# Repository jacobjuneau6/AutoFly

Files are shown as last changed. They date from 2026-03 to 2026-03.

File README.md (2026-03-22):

# AutoFly
A cheap, light and, small autonomus drone with ~100g payload capacity and ardupilot
# Why
I made AutoFly as a successor to a pevious autonomus quadcopter that was not able to fly due to low power budgeting. With bigger motors and a 4X larger battery it should fly perfectly. I have always liked autonomus drones for the simple fact that it focuses entirely on design and tuning compared to FPV drones where the pilot plays a cirtical role.
# Assembly
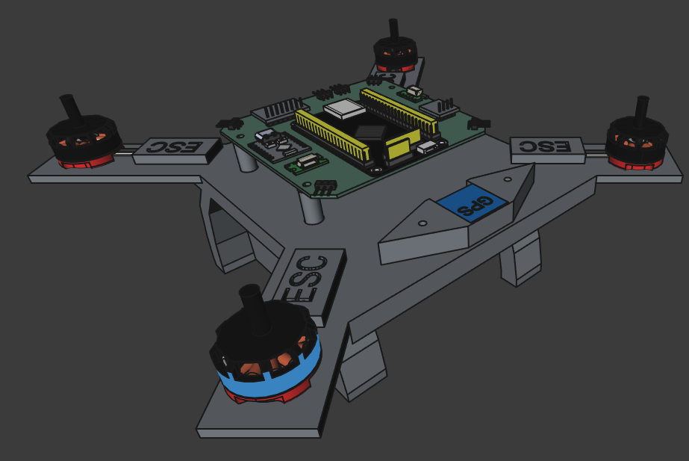
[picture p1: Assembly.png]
assembly photo

# PCB
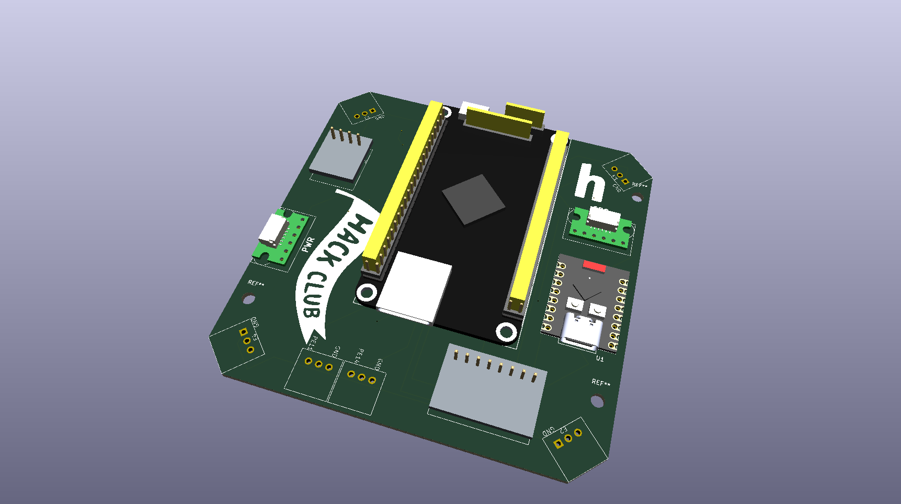
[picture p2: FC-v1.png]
pcb photo

# External Wiring
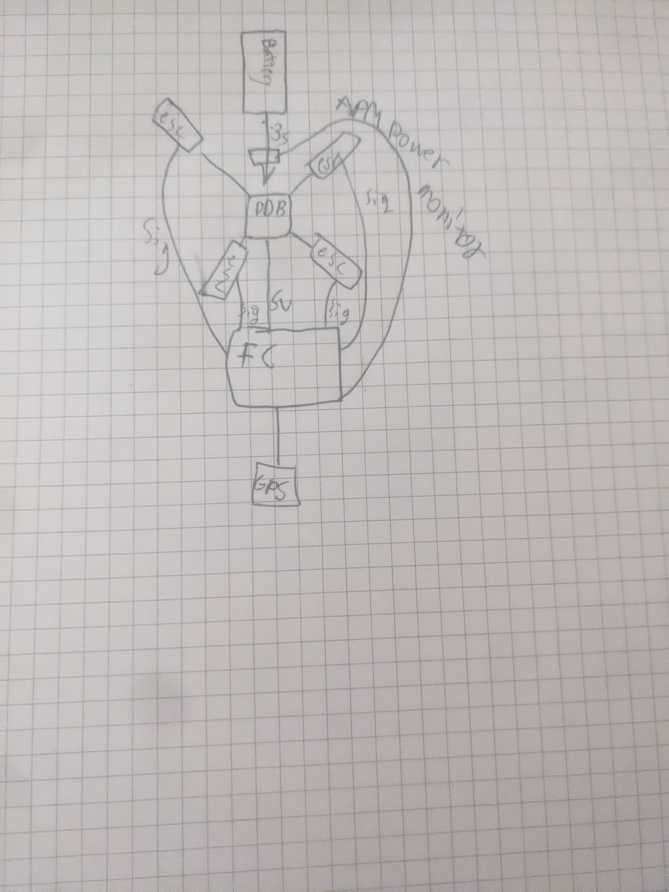
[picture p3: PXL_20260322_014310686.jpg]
hand drawn

# BOM
| Name | Purpose | Quantity | Total Cost (USD) | Link | Distributor |
| --- | --- | --- | --- | --- | --- |
| Custom PCB | hold all of the FC components | 1 | 12.50 |  | PCBWAY |
| Alibaba Shipping Customs and tax | Alibaba Shipping Customs and tax | 1 | 15.45 |  | Alibaba |
| Aliexpress shipping & tax | Aliexpress shipping & tax | 1 | 4.30 |  | Aliexpress |
| Amazon Shipping & TAX | Amazon Shipping & TAX | 1 | 7.67 |  | Amazon |
| M3 screws | hold down various components | 1 | 8.49 | https://www.amazon.com/Self-Tapping-Screws-Phillips-Carbon-Plastic/dp/B0BPM8J5F5 | Amazon |
| Deans T connectors | battery connector | 1 | 1.75 | https://www.aliexpress.us/item/3256806681263722.html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 | Aliexpress |
| 1mm pitch connectors | allows connecting standard drone peripherals to the FC | 1 | 13.22 | https://www.digikey.com/en/products/detail/pololu/4772/19529079 | Digikey |
| APM2.5 power monitor | measures the power and current off the battery to enter failsafe mode when battery about to die | 1 | 9.99 | https://www.amazon.com/Pixhawk-BEC-Helicopter-Quadcopters-Accessories/dp/B0BCJQR3YN?th=1 | Amazon |
| 3S lipo battery | powers the drone | 1 | 14.24 | https://www.amazon.com/OVONIC-Airplane-Quadcopter-Helicopter-Multi-Motor/dp/B077P73SDS?th=1 | Amazon |
| Propellers | provides the motors a way to generate lift | 1 | 16.99 | https://www.amazon.com/uxcell-Propellers-Quadcopter-Airplane-Adapter/dp/B07QK5CXK8 | Amazon |
| Power distribution board | sends power from the battery to all 4 escs | 1 | 4.51 | https://www.aliexpress.us/item/3256806649142265.html?mp=1 | Aliexpress |
| 2205 2300kv brushless motors | allows drone to fly  | 1 | 8.61 | https://www.aliexpress.us/item/3256808432301575.html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 | Aliexpress |
| BLHeli-s 20A ESCs | provides power and control to the motor | 1 | 29.61 | https://www.aliexpress.us/item/2255800001568515.html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 | Aliexpress |
| HGLRC M100-5883 GPS and Compass | Provides location and heading data to the FC | 1 | 18.99 | https://www.amazon.com/HGLRC-M100-5883-GPS-Generation-Compatible/dp/B0CB5N8RQ8 | Amazon |
| ESP32C3 super mini | Provides the transmitter and reciver | 1 | 9.99 | https://www.amazon.com/AITRIP-ESP32-C3-Development-Board-Bluetooth/dp/B0FBGDFPBQ?th=1 | Amazon |
| ICM-42688 IMU | Tells the drone its orientation and acceleration | 1 | 8.39 | https://www.alibaba.com/product-detail/AI-KSEN-Six-Axis-IMU-Module_1601663823996.html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 | Alibaba |
| GY-BMP280 | provides an altimeter | 1 | 0.43 | https://www.alibaba.com/product-detail/GY-BME280-5V-GY-BMP280-5V_1601291648398.html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 | Alibaba |
| STM32H743VIT6 | Will be the brains of the drone | 1 | 11.80 | https://www.alibaba.com/product-detail/STM32H743VIT6-STM32H750VBT6-STM32-STM32H-STM32H7-Core_1601368312109.html | Alibaba |

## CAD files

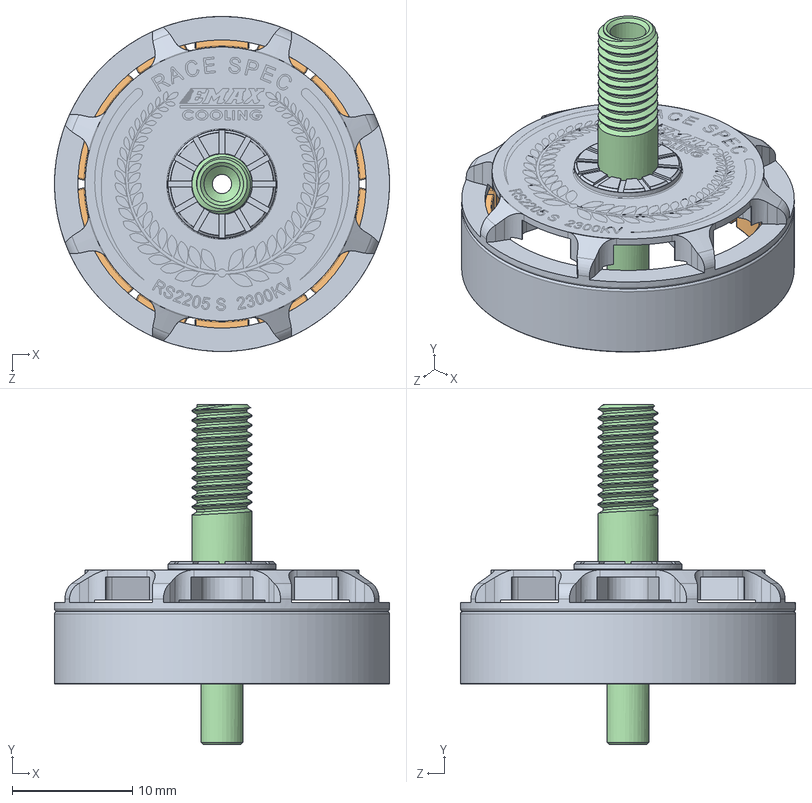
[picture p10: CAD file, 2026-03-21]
CAD/EMAX RS2205 S/ROTOR.SLDASM
27.9 x 28.3 x 27.9 mm
ROTOR BELL
MAGNETS
MAGNETS ADHESIVE
SHAFT

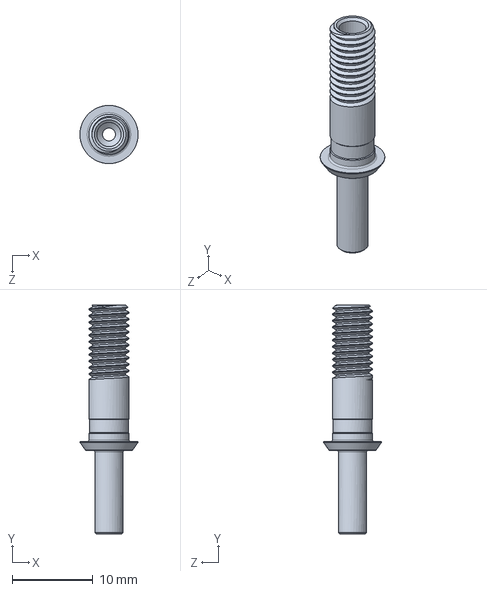
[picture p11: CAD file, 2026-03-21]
CAD/EMAX RS2205 S/SHAFT.SLDPRT
7.20 x 28.3 x 7.20 mm

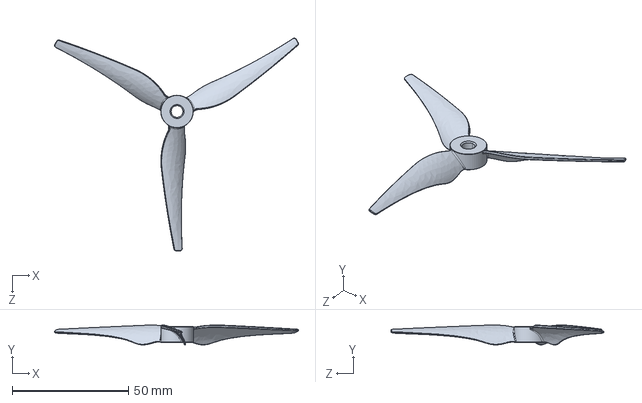
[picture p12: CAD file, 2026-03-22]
CAD/uploads_files_5648372_Gemfan+Propeller+51466.STEP
105.0 x 8.54 x 91.6 mm

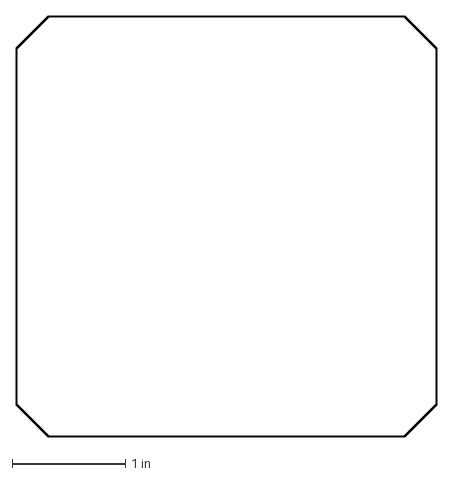
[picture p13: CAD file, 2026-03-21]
FC-v1/FC-v1/exports/DXF/FC-v1-Edge_Cuts.dxf
3.72 x 3.72 in

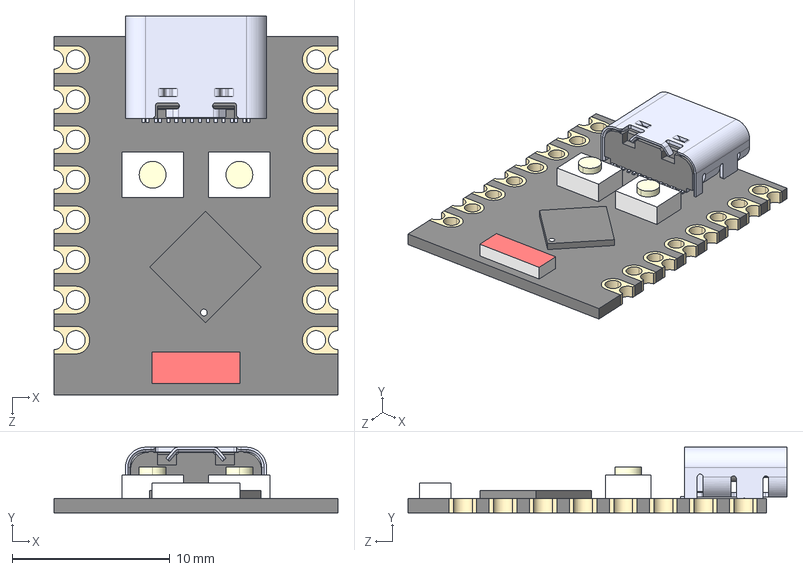
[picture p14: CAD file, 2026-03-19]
FC-v1/FC-v1/symbols/ESP32-C3 SuperMini_TH--3DModel-STEP-56544.STEP
18.0 x 4.16 x 24.0 mm
Board c3mini
USB C
components (other)^ESP32-C3 SuperMini

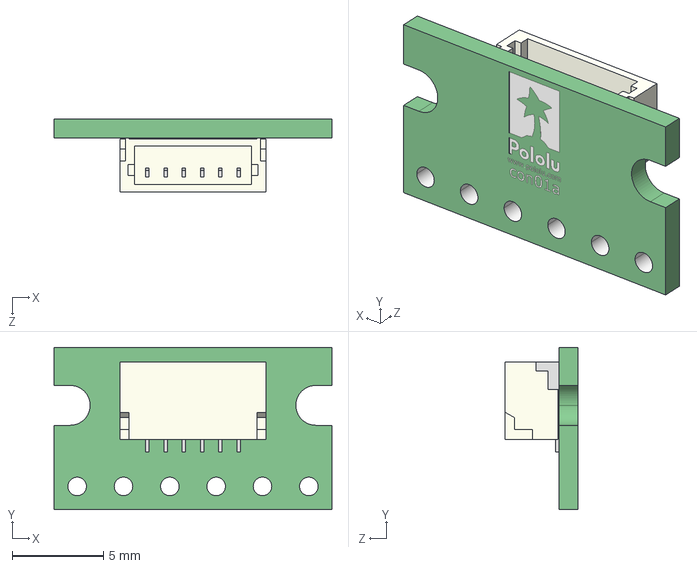
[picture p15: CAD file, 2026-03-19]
FC-v1/FC-v1/symbols/pololu-4770-4771-4772-4773-models/breakout-for-jst-sh-style-connector-6-pin-male-side-entry.step
15.2 x 8.89 x 3.98 mm

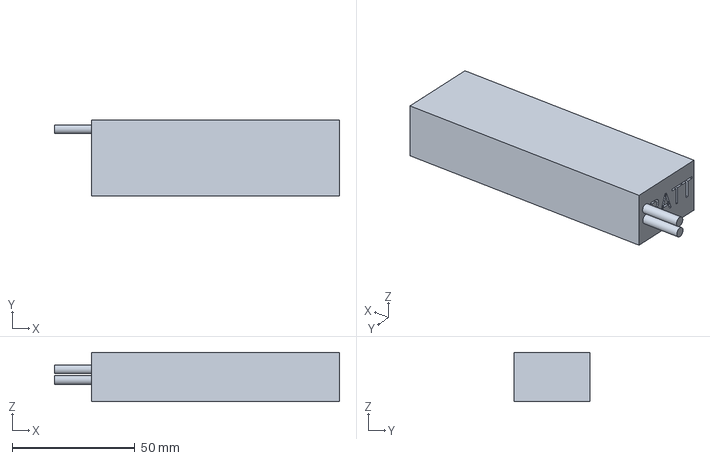
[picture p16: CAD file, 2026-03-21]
CAD/Battery.FCStd
116.0 x 31.0 x 20.0 mm

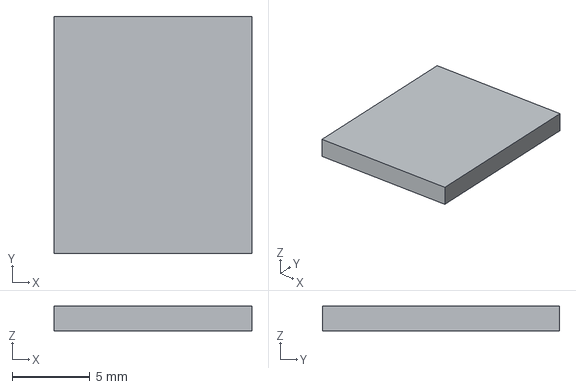
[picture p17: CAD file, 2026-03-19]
FC-v1/FC-v1/symbols/bmp.step
12.7 x 15.2 x 1.60 mm

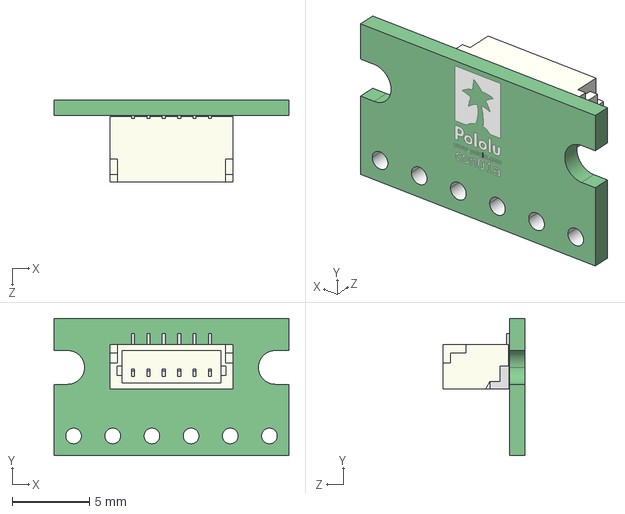
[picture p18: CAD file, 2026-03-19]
FC-v1/FC-v1/symbols/pololu-4770-4771-4772-4773-models/breakout-for-jst-sh-style-connector-6-pin-male-top-entry.step
15.2 x 8.89 x 5.34 mm

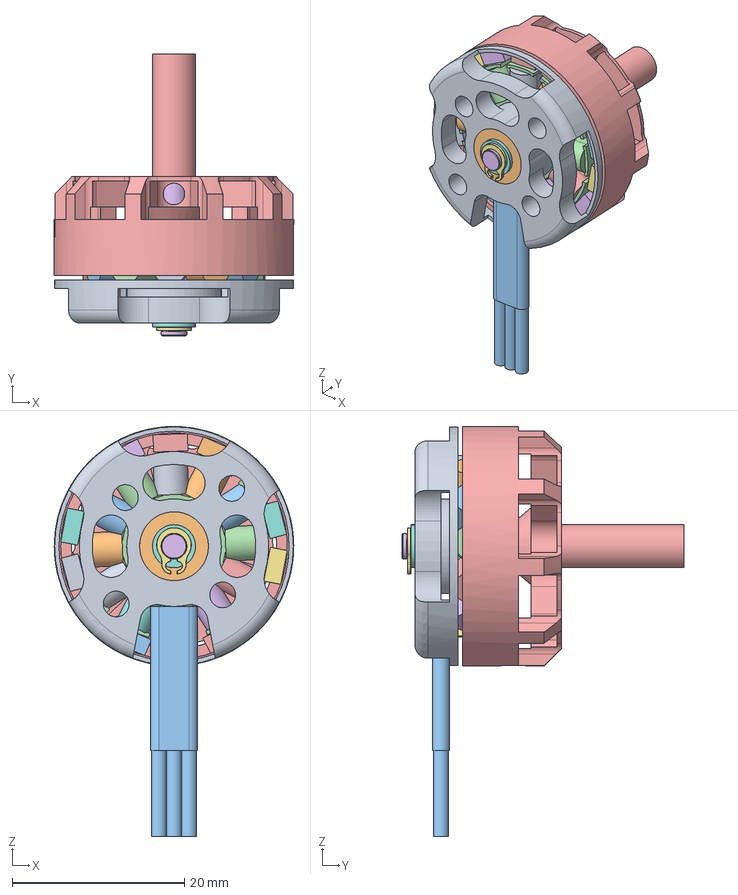
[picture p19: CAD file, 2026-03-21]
CAD/2205.FCStd
27.8 x 32.8 x 47.7 mm
BASE
BEARING
BEARING001
STATOR
CAN
SHAFT
98541A111_External Retaining Ring
SPACER
COILS
COILS001
COILS002
COILS003
COILS004
COILS005
COILS006
COILS007
COILS008
COILS009
COILS010
COILS011
Magnets
Magnets001
Magnets002
Magnets003
Magnets004
Magnets005
Magnets006
Magnets007
Magnets008
Magnets009
Magnets010
Magnets011
Magnets012
Magnets013
Cable Sleeve

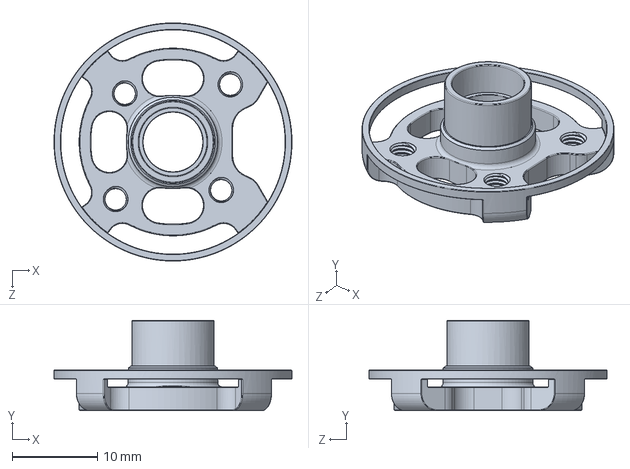
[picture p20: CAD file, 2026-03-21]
CAD/EMAX RS2205 S/STATOR.SLDPRT
27.9 x 10.6 x 27.9 mm

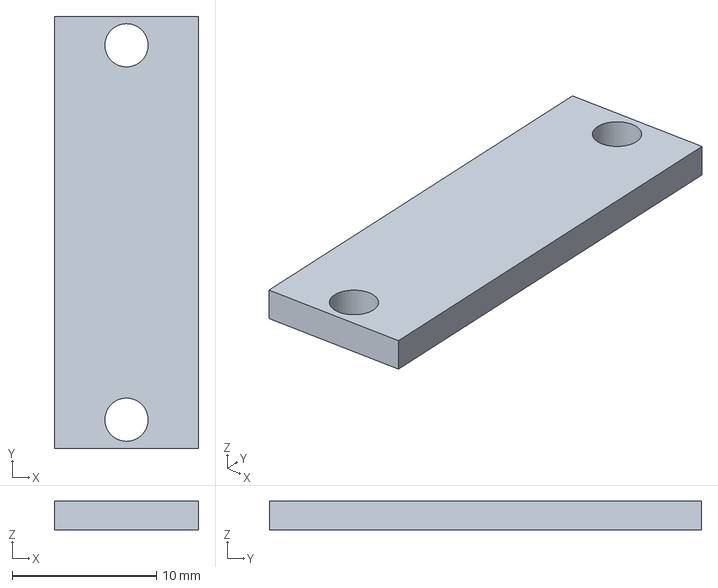
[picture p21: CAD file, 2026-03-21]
CAD/BatteryCase.FCStd
10.0 x 30.0 x 2.00 mm

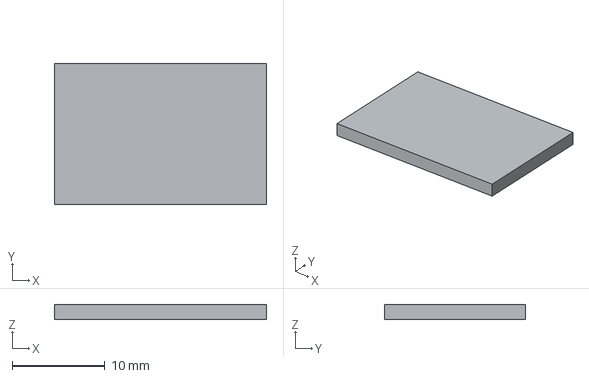
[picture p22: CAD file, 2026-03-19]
FC-v1/FC-v1/symbols/icm.step
22.9 x 15.2 x 1.60 mm

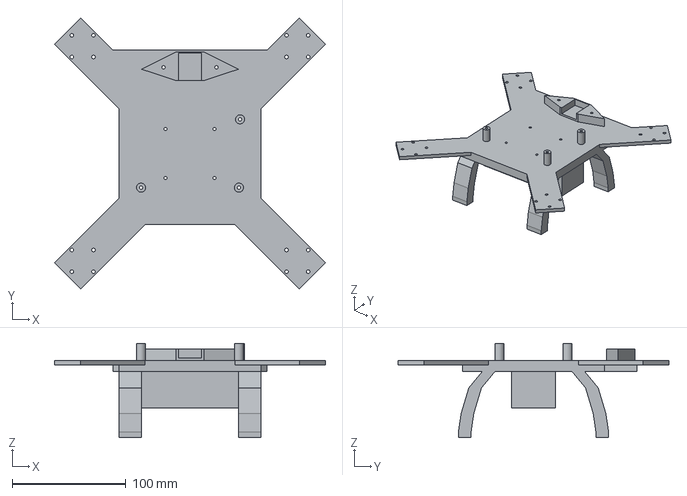
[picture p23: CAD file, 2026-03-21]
CAD/chassis-v1-Body.step
238.1 x 238.1 x 83.0 mm

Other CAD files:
CAD/assembly.FCStd
CAD/EMAX RS2205 S/MAGNETS ADHESIVE.SLDPRT
FC-v1/FC-v1/symbols/SMT32H7(50VBT6)_DevEBox_Board.iges
CAD/697f6b56e4acdd526a510600.step
CAD/CAD.3mf
CAD/EMAX RS2205 S/BEARING.sldprt
CAD/EMAX RS2205 S/MAGNETS.SLDPRT
CAD/EMAX RS2205 S/SCREW.SLDPRT
CAD/EMAX RS2205 S/STATOR SLEEVE.SLDPRT
CAD/EMAX RS2205 S/WASHER.SLDPRT
CAD/EMAX RS2205 S/WINDING.SLDPRT
CAD/ESC.FCStd
CAD/FC-v1.FCStd
CAD/GPS.FCStd
CAD/XT60.FCStd
CAD/chassis-v1.FCStd
FC-v1/FC-v1/exports/DXF/FC-v1-B_Mask.dxf
FC-v1/FC-v1/exports/DXF/FC-v1-F_Mask.dxf
FC-v1/FC-v1/symbols/0530470610--3DModel-STEP-231308.STEP
FC-v1/FC-v1/symbols/530470610/530470610.step
FC-v1/FC-v1/symbols/SMT32H7(50VBT6)_DevEBox_Board.stl

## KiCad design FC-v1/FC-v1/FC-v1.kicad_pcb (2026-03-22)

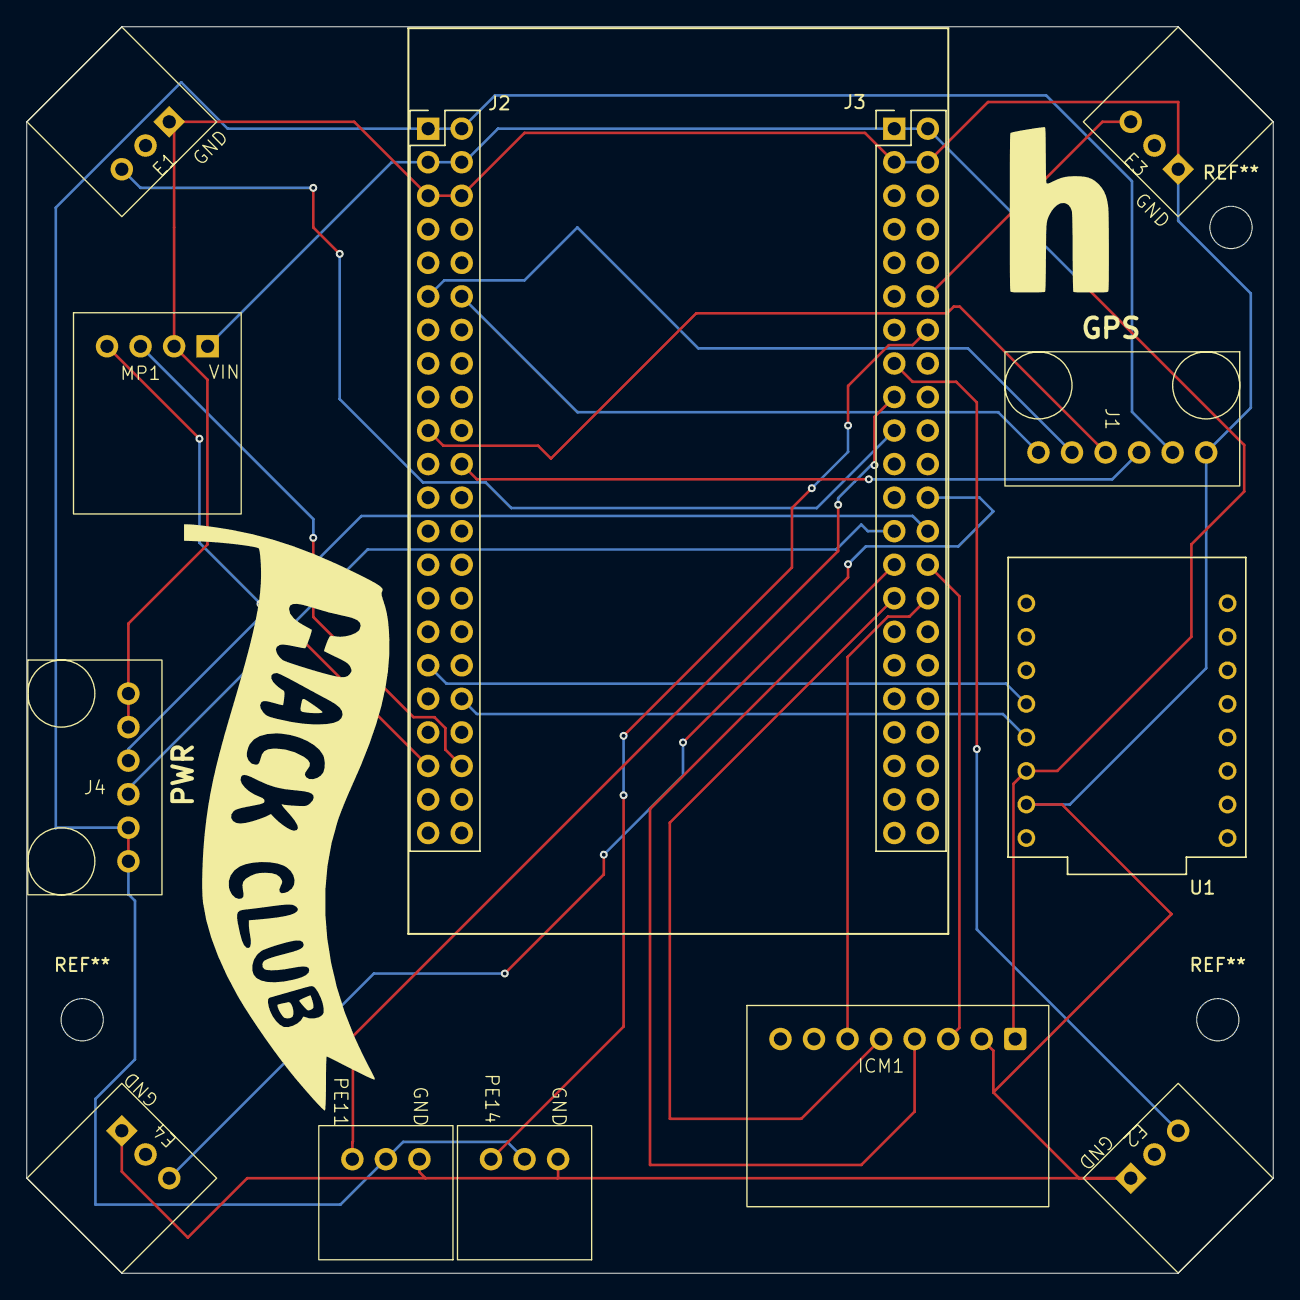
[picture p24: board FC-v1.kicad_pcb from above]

Board: 2 copper layers, 94.4 x 94.4 mm, 13 parts (0 on the bottom side), 23 nets.

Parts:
E1, E2, E3, E4: ESC-connector
ICM1: ICM42688
J1, J4: 530470610; 4772
J2: Left; PinHeader_2x22_P2.54mm_Vertical
J3: Right; PinHeader_2x22_P2.54mm_Vertical
MP1: BMP280
U1: ESP32-C3_SUPERMINI_TH; MODULE_ESP32-C3_SUPERMINI_TH
U2, U3: Untitled

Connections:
+3.3V: ICM1.1 (VCC), J2.3, J2.4, J3.1, J3.2, MP1.1 (VIN), U1.3.3 (3V3)
+5V: J1.2, J2.1, J2.2, J4.5, J4.6, U2.2 (5V), U3.2 (5V)
/PA4: ICM1.6 (CS), J3.30
/PA5: ICM1.5 (SCLK), J3.29
/PA6: ICM1.3 (MISO), J3.28
/PA7: ICM1.4 (MOSI), J3.27
/PA9_TX1: J1.4, J2.19
/PA10_RX1: J1.3, J2.22
/PB0: E4.1 (SIGNAL), J3.24
/PB6: J2.40, MP1.3 (SCl)
/PB7: J2.39, MP1.4 (SDA)
/PB10: E3.1 (SIGNAL), J3.12
/PC4: J3.26, J4.3
/PC5: J3.25, J4.4
/PD6: J2.33, U1.3 (GPIO3)
/PD7: J2.36, U1.4 (GPIO4)
/PD12: J1.6, J2.12
/PD13: J1.5, J2.11
/PE9: E1.1 (SIGNAL), J3.19
/PE11: J3.17, U2.3 (SIG)
/PE13: E2.1 (SIGNAL), J3.15
/PE14: J3.14, U3.3 (SIG)
GND: E1.2 (GND), E2.2 (GND), E3.2 (GND), E4.2 (GND), ICM1.2 (GND), J1.1, J2.5, J2.6, J3.3, J3.4, J4.1, J4.2, MP1.2 (GND), U1.G (GND), U2.1 (GND), U3.1 (GND)

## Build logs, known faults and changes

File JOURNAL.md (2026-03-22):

<!--
  This journal is auto generated by Stasis.
-->

# 3/21/2026 2 PM - Chassis strength testing

_Time spent: 2h_

I decided that it would be best to print the chassis upsidedown in order to allow the landing legs to be able to fold out in the event of a crash. I also adjusted infill settings to get it as light as possible while still maintaining structure going with 10% grid infill with 30% gyroid on the landing legs.
I printed a test chassis in order to perform structural testing. i did this testing by setting the chassis on the ground and dropping a 0.5KG weight from higher and higher. The landing legs failed after the 3meter drop test so i know that the legs are fine up to ~38N.








# 3/21/2026 4 AM - Drone CAD part 2

_Time spent: 3.25h_

I decided after considering all positions to have the battery connections come out the left side and to have a wire loop pigtail there. This was done to minimize the EMF from the battery cables manipulating the magnetometer.

I also added the first version of the landing gear, a simple design that i have used before on lighter drones. In my next log, i will decided how i am going to print the drone and print one then do structural testing. I used shorter stubby legs due to the low mass nature of this drone and the relativly high throttle curve that i want to use during landing. I also designed a battery retention clip that will be screwed in, holding the battery securly.












# 3/20/2026 5 AM - Drone CAD part 1

_Time spent: 4h_

I researched the magnetic interference i could expect fron a 3s system and decided the optimal place to put the magnetometer was right inbetween the front 2 motors back a bit.

I then after figuring this out designd a flat little chassis that hols the power distribution board and the motors and the FC. I plan to design the landig gear and battery/payload holder later.


Form prevoius projects, my motormounts my need some thickening to be strong enough. 
I plan to zip tie the ESCs down as i cannot plan for exactly how much wire i will have and where they will end up.




# 3/19/2026 6 AM - Motor, Battery and, ESC selection

_Time spent: 5h_

I firsh stared with a 2S 5200mAh 50C lipo battery as it is what i have used on previous aerial vehicles and I understand its performace curve and voltage drop quite well. However as i began running the numbers, i realized that loaded with my standard 5"x3" bivane propellers that it would max out at about 6K RPMs which would not produce nearly enough thrust for stable flight and could cause problems in even slight wind. For these calculations, i am assuming 2300kv brushless motros becuase of their relavtivly high efficency compared to weight. I decided to use 20A ESCs due to their lower cost and to avoid overstressing the battery. If i switch to a 3S 2200mAh 50C lipo, I loose some flight time, ~20mins total, however, i produce more thrust and end up being more stable with ~16k RPMs Something else i may try once i have the drone bult is using 3d printed toroidal propellers as they are quieter and lighter.








# 3/18/2026 2 AM - FC PCB design and DRC

_Time spent: 6h_

I added the GPS and power module connectors which took a while because i could not find the pin pitch so i had to measure a connector that i already have to se the correct size.
I sized and routed the PCB with took the majority of the time due to the almost 100 connections that had to be made


i had to use many vias because i needed to keep everything roughly balanced for it to be able to fly and i ended up having multiple crosses over the the same copper layer

I am a bit aprehensive about using vias because with some previous boards i have shored out vias that are right next to a connecting while soldering.

In addition, i also imported the 3d models of the parts into kicad to get the 3d view. I was unable to find actual 3d models of the BMP280 and ICM42688 so i used blank rectangles in their dimensions instead



I also stared thinking about ESCs and motors. I want ESCs that run BlHeli_S firmware due to their support for digital speed protocols and telemetry capabilities and i am going for 20A ESCs due to their lower heat output making them easer to mount




# 3/17/2026 4 PM - GPS,Power and Motor connections

_Time spent: 2h_

I decided to use the HGLRC M100-5883 GPS/Compass module on my drone because it not only contains a GPS module but also a Compass
I added the GPS,Power and Motor connections to my schematic as well as wiring everything up







# 3/17/2026 2 AM - Added esp32 transmitter and bmp280 altimeter

_Time spent: 2h_

I added the bmp280 altimeter to the scematci and connected its pins
I am closely folowing the     NxtPX4v2 FC board for wiring as uses thew same MCU as I am
I wired up the esp32c3 transmitter to the STM32 and verified pin compatibilty








# 3/16/2026 2 PM - Adding the IMU to my Flight Controller

_Time spent: 1.333333333333333h_

I researched the available SPI busses on the stm32 and i decided to use SPI1 for the IMU
I Decided on my exact pin connections after reading the datasheet
I Connected everything in the schematic








# 3/16/2026 5 AM - Flight Controler Design

_Time spent: 3h_

- I have decided to design my flight control board first, then design the rest of the drone making sure to keep the FC as light and as small as possible
- The FC consists of a few items

1. The STM32H743VIT6dev board which provides the MCU and the microsd card slot
2. The ICM-42688 IMU breakout that provides orientation data
3. An ESP32C3 that provides remote telemetry
4. Connection to the GPS/Compass and connection the the power monitor
- So far i have found the footprints and schematic symbols for  the stm32 board and the esp32 co-processor
- I would also like to have an onboard altimiter, the BMP280 so that it can meausure the barometric pressure.







# 3/16/2026 3 AM - Research for the main board and basic planning

_Time spent: 3h_

- I am creating this project because i want to be able to survey large areas autonomously.
- I have decided that I will use [Ardupilot](https://ardupilot.org/ardupilot/) as the base formware for this project as i have some familiarity with it from helping a friend get their autonomous boat running.
- For cost and design reasons i have decied that i will use the STM32H743VIT6 as my main MCU and a BMI160 as my IMU
- The STM32H743VIT6 is optimal for this concept becuase it provides 1MB of flash space and enought compute power for a drone at 480Mhz as well as that it is an already common chip in Ardupilot FCs
- I chose the BMI160 because it is reliable, easy to source and relativley cheap while also being already supported by Ardupilot




- I also sketched out the basic idea for this drone with 4 motors and a battery in the center underneath the main control board

PXL_20260316_012353842.MP

- I will be integrating the MCU and IMU as development boards rather than the indiviadual chips as it is more cost effective and allows for less risk to be taken on the main PCB design.





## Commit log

2026-03-19 design and build PCB
    [0530470610--3DModel-STEP-231308.STEP, 530470610.step, ESP32-C3 SuperMini_TH--3DModel-STEP-56544.STEP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]
2026-03-21 CAD files
    [2205.FCStd, 697f6b56e4acdd526a510600.step, BEARING.sldprt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]
2026-03-22 Journal BOM Readme Gerbers
    [AutoFly-bom.csv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]
